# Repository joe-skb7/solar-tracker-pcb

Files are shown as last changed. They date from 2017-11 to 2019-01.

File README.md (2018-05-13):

# Solar tracker PCB

This project contains solar tracker PCB I made for my dad's project.

3D Model, Front View:

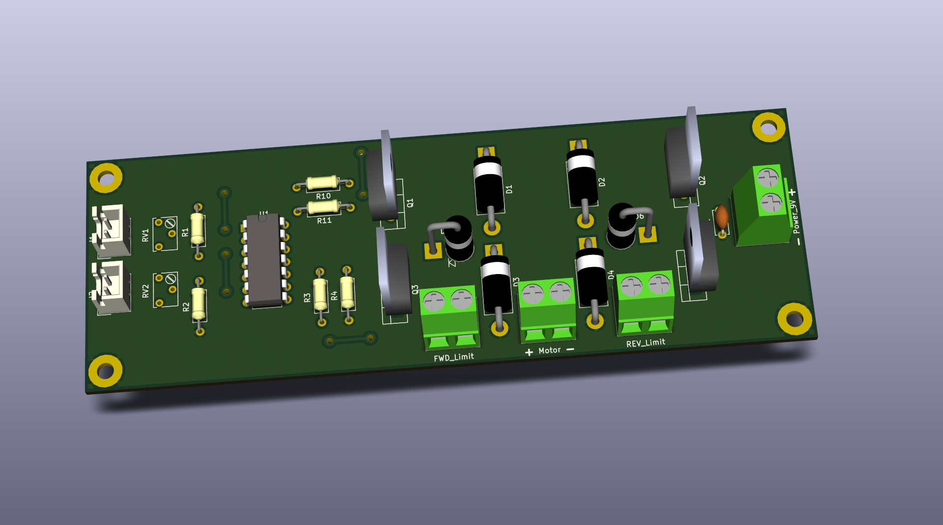
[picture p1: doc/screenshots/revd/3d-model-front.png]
3D Model, Front View


3D Model, Bottom View:

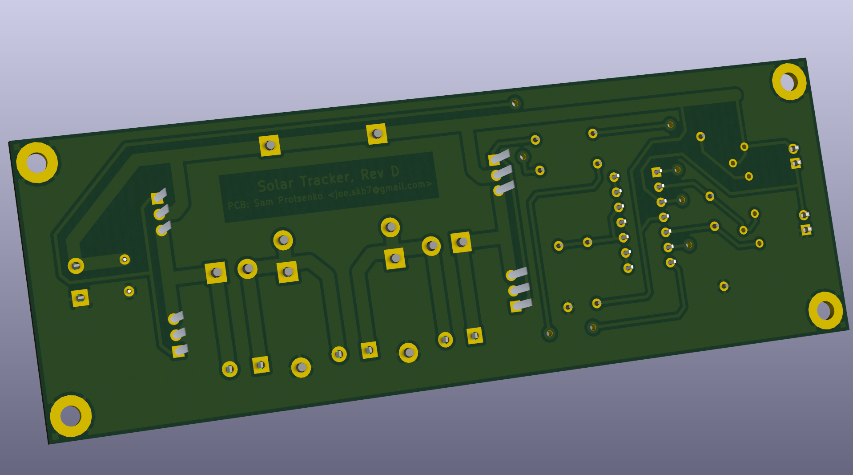
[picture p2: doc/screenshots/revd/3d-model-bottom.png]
3D Mode, Bottom View


Schematic:

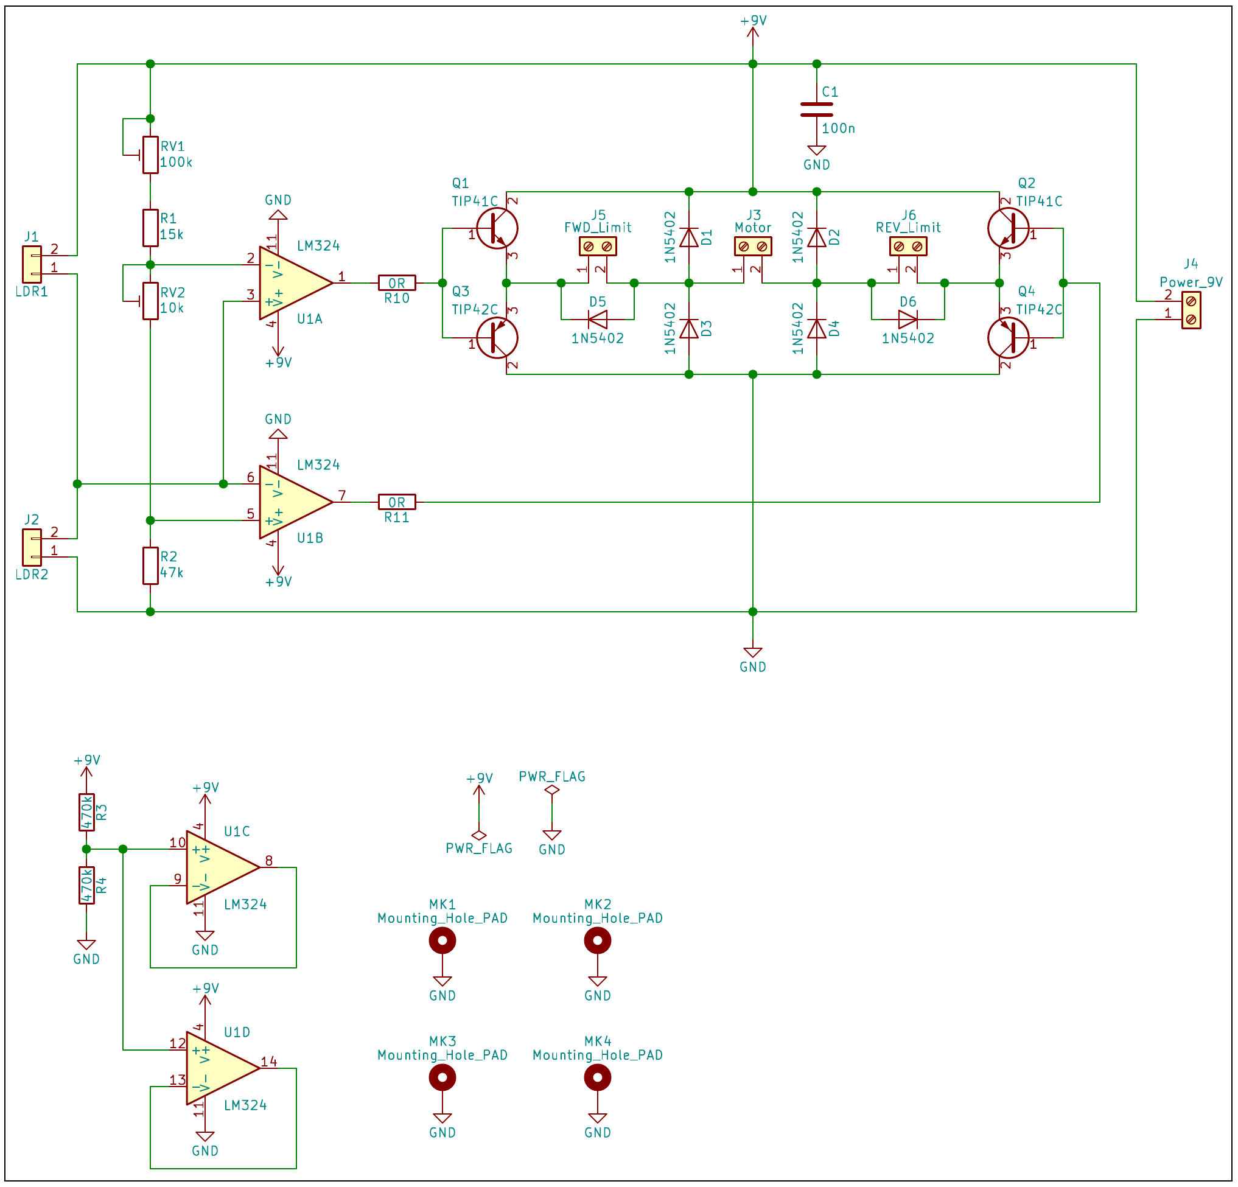
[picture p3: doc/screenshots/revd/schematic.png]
Schematic


I used KiCAD 4.0.7 for this PCB, but it should open fine in different versions,
as I keep `-cache.lib` file in this repo.

Original schematic can be found in `doc/scheme.jpg`. Things that I changed:
* properly terminated unused OPAMP parts
* added limit switches connection

## Schematic explanation

LDR1 and LDR2 photo-resistors yield signal which is used to determine in which
direction PV unit (solar panel) should be rotated, i.e. in which direction
we have more light radiation.

Signal from photo-resistors is being compared further by comparators built on
U1A and U1B OPAMPs. Reference voltage level is generated by dividers built on
R1, R2 resistors and RV1, RV2 trim-pots.

RV1 trim-pot is used to adjust this reference voltage point, so that motor
stands still when both photo-resistors are receiving the same light level.
RV2 is used to setup hysteresis level, so that motor is not moving when the
light difference on photo-resistors is small.

H-bridge formed by Q1-Q4 transistors is powering the motor, according to control
signals from comparators. Transistors are working in switch mode, as comparators
yield only 0 or VCC:

    V_out = 0,   if V+ < V-
    V_out = Vcc, if V+ > V-

D1-D4 are just flyback diodes, providing the path for back EMF discharge from
motor's coil, preventing other elements from it (transistors can be burnt, or
limit switches can be carbonized due to arcing).

C1 provides some of the energy required by the motor during the initial spike of
each turn-on.

R3 and R4 are used to properly terminate unused OPAMPs (U1C, U1D).

J5 and J6 terminal blocks (along with D5, D6 diodes) are used for connecting the
limit switches.

### Power consideration

Power voltage: 9V must be used. It's because the motor will receive only
`Vcc - 2.6` Volts, due to voltage drop across transistors and also on OPAMP,
as it's not Rail-to-Rail one. MG995 requires the voltage to be 4.8V ... 7.2V,
so the voltage drop must be accounted for.

Power current: 2A or more. Because MG995 can consume up to 1.5A on start
("stall current").

In case when 12V battery is used (it's common in solar panels appliance),
I suggest one to use external 12V-to-9V buck converter (2A rated, or more). It's
efficient (95%), small enough, and usually costs only $2-$3. No need to
over-complicate tracker schematic by adding voltage regulator scheme to it.

### Limit switches

`doc/limit-switch/` directory contains two possible schemes to implement limit
switches in H-bridge, with pros/cons overview. I personally like the second
scheme the best, so I implemented it in this project.

### EMI note

Notice that switching of DC motor's brushes leads to EMI, which may affect your
external circuits (especially digital ones, like MCUs). In that case you should
install EMI suppressor on your motor leads.

## Prepared files

`out/` directory contains ready to use files for manufacturing the PCB.

### Toner Transfer Method

See `out/toner-transfer-method/` for ready to use files.

Notes:
1. Remove the copper pour from both sides of PCB
2. Notice the Vias and front layer tracks. You need to solder jumper wires
   instead of them, in case if you are using single sided copper clad board.

### Manufacturing at plant

You can order the PCB to be manufactured on plant, e.g. at Seeed Studio (Fusion
PCB) or JLCPCB. Gerber files and drill file are prepared at `out/gerber/`.

## References

### Original scheme description and discussion

[1] http://www.electroschematics.com/8019/diy-solar-tracker-system/

[2] http://izobreteniya.net/solnechnyiy-treker-svoimi-rukami/

[3] http://radiokot.ru/forum/viewtopic.php?f=3&t=144321

[4] https://www.youtube.com/watch?v=UQyiuxo1Wvo

### Unused OPAMPs: proper termination

[5] https://www.electronicproducts.com/Analog_Mixed_Signal_ICs/Amplifiers/Properly_terminating_an_unused_op_amp.aspx

### EMI suppressor

[6] http://reprap.org/wiki/GM3_Noise_Suppressor_v1.0

## Authors

**Sam Protsenko**

## License

This project is licensed under the GPLv3.

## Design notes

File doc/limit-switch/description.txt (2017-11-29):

limit-switch-1.png
------------------

Pros:
 1. Easier to implement
 2. Limit switches can be low power rated

Cons:
 1. Transistor bases are floating in the air, when limit switch is activated;
    at least bases need to be pulled down
 2. Not a robust scheme: if transistor is broken, limit switch won't work

limit-switch-2.png
------------------

NOTE: flyback diodes are placed right next to motor, as they are for protecting
      the rest of the scheme from motor's back EMF. This way we can choose
      limit switches diodes for smaller voltage.

Pros:
 1. Robust scheme; limit switches are in motor circuit, so they will always
    work (even if transistors are broken)
 2. No need to pull-down transistors' bases

Cons:
 1. Limit switches must be high-power rated (big current)
 2. Additional two diodes are needed

We choose "limit-switch-2.png" option, as it's more robust and commonly adopted.

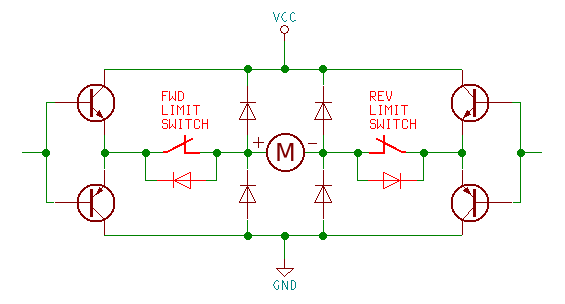
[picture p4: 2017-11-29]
doc/limit-switch/limit-switch-2.png

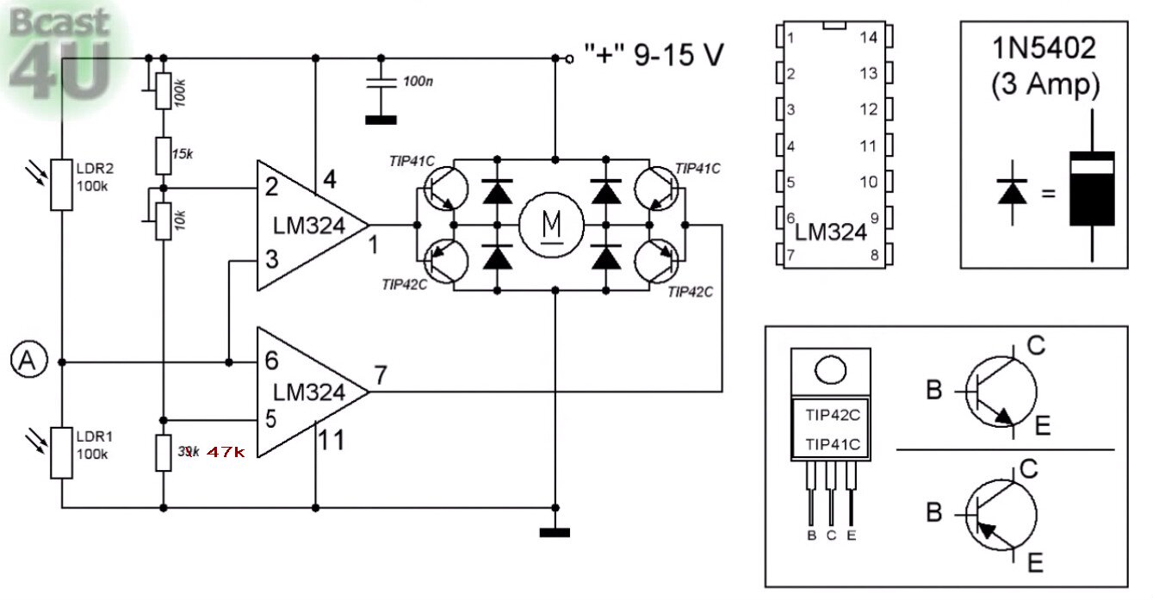
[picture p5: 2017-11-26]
doc/scheme.jpg

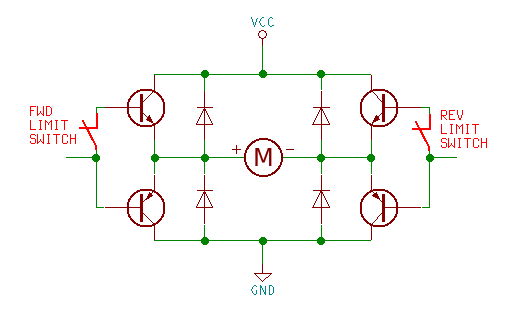
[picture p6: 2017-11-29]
doc/limit-switch/limit-switch-1.png

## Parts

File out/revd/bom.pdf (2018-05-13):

solar-tracker

Id | Designator | Package | Quantity | Designation
1 C1 | | C_Disc_D5.0mm_W2.5mm_P5.00mm | 1 100n
2 D1-D6 | | D_DO-201AD_P15.24mm_Horizontal | 6
3 J1,J2 | | JST_XH_B02B-XH-A_02x2.50mm_Straight | 2
4 J3-J6 | | TerminalBlock_Pheonix_MKDS1.5-2pol | 4
5 Q1,Q2 | | TO-220_Vertical | 2 TIP41C
6 Q3,Q4 | | TO-220_Vertical | 2 TIP42C
7 R1 | | R_Axial_DIN0207_L6.3mm_D2.5mm_P10.16mm_Horizontal | 1 15k
8 R10,R11 | | R_Axial_DIN0207_L6.3mm_D2.5mm_P10.16mm_Horizontal | 2 0R
9 R2 | | R_Axial_DIN0207_L6.3mm_D2.5mm_P10.16mm_Horizontal | 1 47k
10 R3,R4 | | R_Axial_DIN0207_L6.3mm_D2.5mm_P10.16mm_Horizontal | 2 470k
11 RV1 | | Potentiometer_Trimmer_Bourns_3266W | 1 100k
12 RV2 | | Potentiometer_Trimmer_Bourns_3266W | 1 10k
13 U1 | | DIP-14_W7.62mm | 1 LM324

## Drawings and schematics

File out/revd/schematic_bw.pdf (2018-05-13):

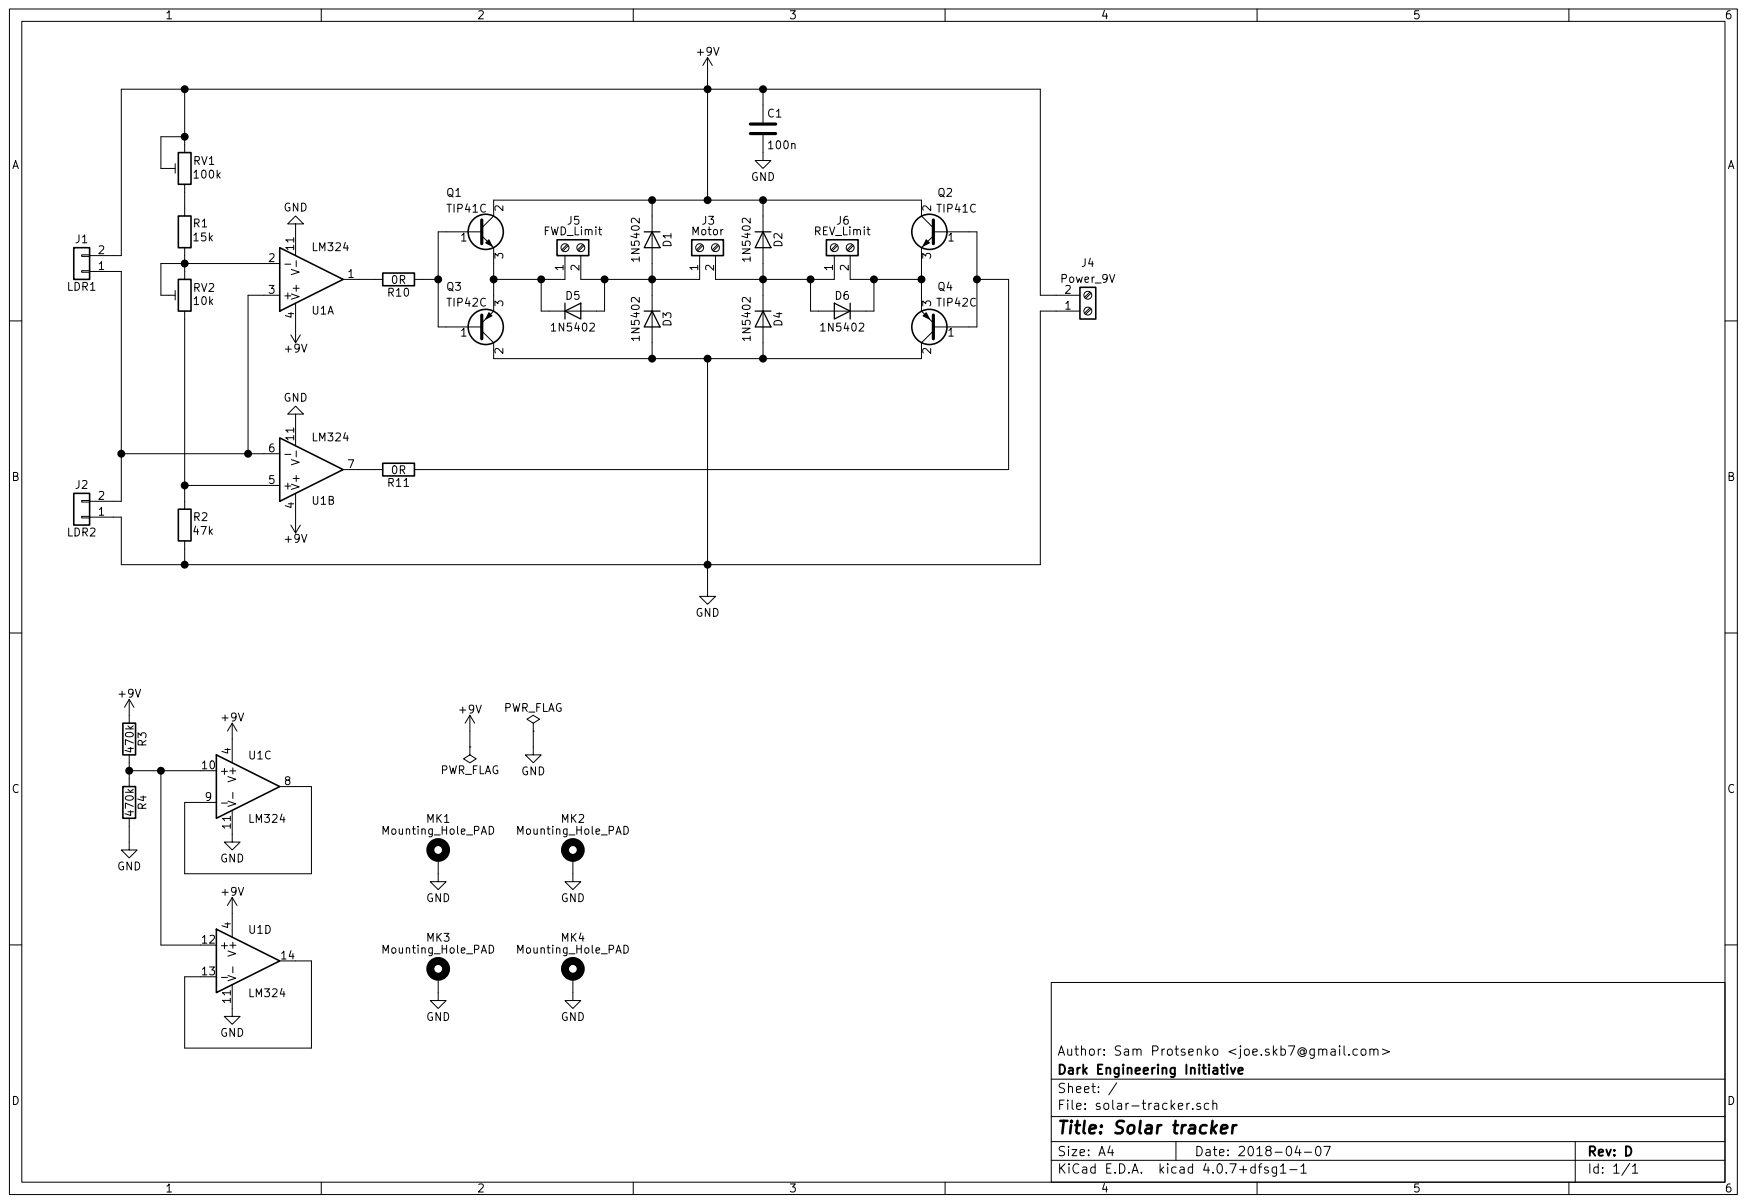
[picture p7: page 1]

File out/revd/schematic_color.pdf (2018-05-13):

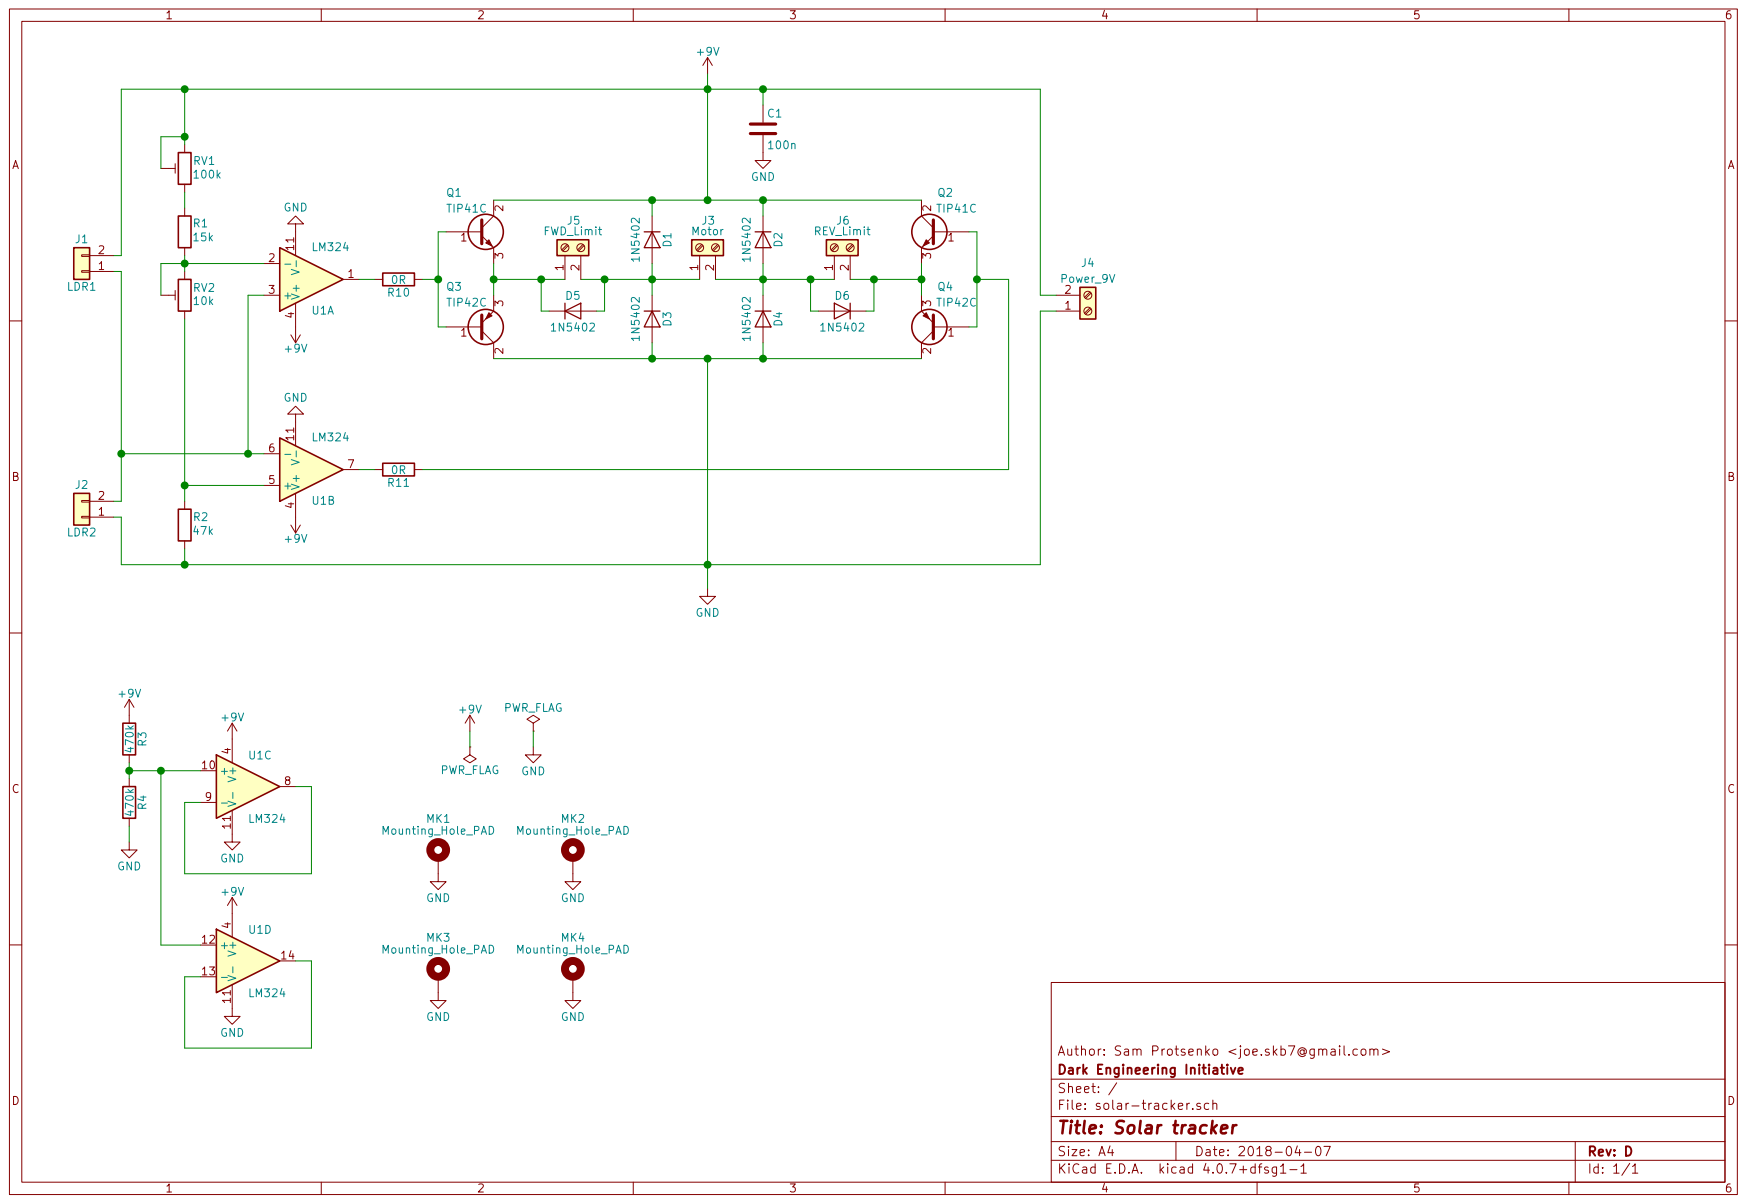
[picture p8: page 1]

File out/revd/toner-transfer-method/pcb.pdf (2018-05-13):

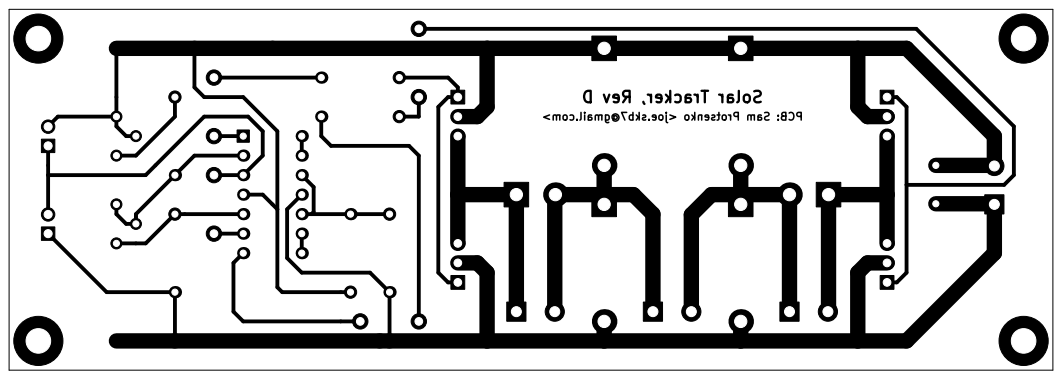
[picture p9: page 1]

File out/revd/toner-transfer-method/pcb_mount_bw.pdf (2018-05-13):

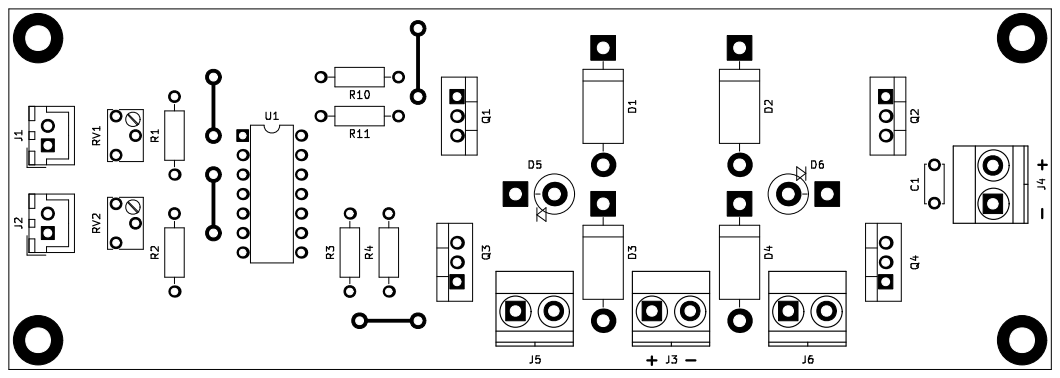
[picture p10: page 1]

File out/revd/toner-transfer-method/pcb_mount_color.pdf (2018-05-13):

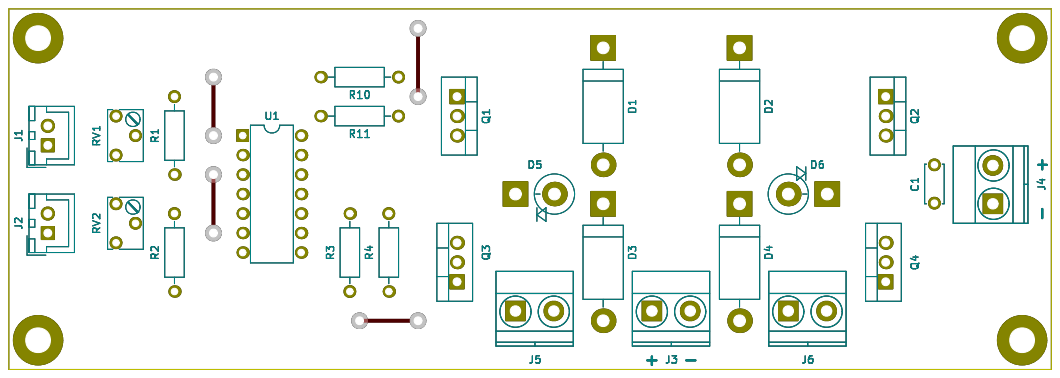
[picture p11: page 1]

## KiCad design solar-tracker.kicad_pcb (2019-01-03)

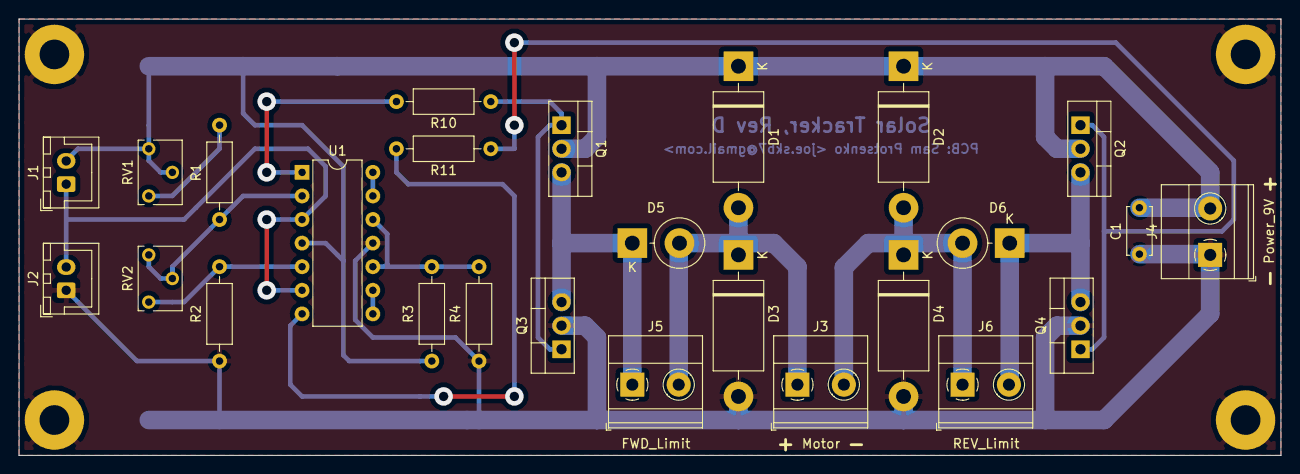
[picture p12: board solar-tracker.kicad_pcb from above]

Board: 2 copper layers, 135.9 x 47.0 mm, 30 parts (0 on the bottom side), 17 nets.

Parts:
C1: 100n; C_Disc_D5.0mm_W2.5mm_P5.00mm
D1, D2, D3, D4: 1N5402; D_DO-201AD_P15.24mm_Horizontal
D5, D6: 1N5402; D_DO-201AD_P5.08mm_Vertical_KathodeUp
J1: LDR1; JST_XH_B02B-XH-A_1x02_P2.50mm_Vertical
J2: LDR2; JST_XH_B02B-XH-A_1x02_P2.50mm_Vertical
J3: Motor; TerminalBlock_Phoenix_MKDS-1,5-2_1x02_P5.00mm_Horizontal
J4: Power_9V; TerminalBlock_Phoenix_MKDS-1,5-2_1x02_P5.00mm_Horizontal
J5: FWD_Limit; TerminalBlock_Phoenix_MKDS-1,5-2_1x02_P5.00mm_Horizontal
J6: REV_Limit; TerminalBlock_Phoenix_MKDS-1,5-2_1x02_P5.00mm_Horizontal
MK1, MK2, MK3, MK4: Mounting_Hole_PAD; MountingHole_3.2mm_M3_Pad
Q1, Q2: TIP41C; TO-220-3_Vertical
Q3, Q4: TIP42C; TO-220-3_Vertical
R1: 15k; R_Axial_DIN0207_L6.3mm_D2.5mm_P10.16mm_Horizontal
R2: 47k; R_Axial_DIN0207_L6.3mm_D2.5mm_P10.16mm_Horizontal
R3, R4: 470k; R_Axial_DIN0207_L6.3mm_D2.5mm_P10.16mm_Horizontal
R10, R11: 0R; R_Axial_DIN0207_L6.3mm_D2.5mm_P10.16mm_Horizontal
RV1: 100k; Potentiometer_Bourns_3266W_Vertical
RV2: 10k; Potentiometer_Bourns_3266W_Vertical
U1: LM324; DIP-14_W7.62mm

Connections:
+9V: C1.1, D1.1, D2.1, J1.2, J4.2, Q1.2, Q2.2, R3.1, RV1.1, RV1.2, U1.4
GND: C1.2, D3.2, D4.2, J2.1, J4.1, MK1.1, MK2.1, MK3.1, MK4.1, Q3.2, Q4.2, R2.2, R4.2, U1.11
unnamed: D1.2, D3.1, D5.2, J3.1, J5.2
unnamed: D2.2, D4.1, D6.2, J3.2, J6.1
unnamed: D5.1, J5.1, Q1.3, Q3.3
unnamed: D6.1, J6.2, Q2.3, Q4.3
unnamed: J1.1, J2.2, U1.3, U1.6
unnamed: Q1.1, Q3.1, R10.1
unnamed: Q2.1, Q4.1, R11.1
unnamed: R1.1, RV1.3
unnamed: R1.2, RV2.1, RV2.2, U1.2
unnamed: R2.1, RV2.3, U1.5
unnamed: R3.2, R4.1, U1.10, U1.12
unnamed: R10.2, U1.1
unnamed: R11.2, U1.7
unnamed: U1.8, U1.9
unnamed: U1.13, U1.14

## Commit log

2017-11-25 Add initial KiCAD files
    [solar-tracker.kicad_pcb, solar-tracker.sch]
2017-11-26 Started routing the PCB layout
    [solar-tracker.kicad_pcb, solar-tracker.sch]
2017-11-26 doc: Add original schematic
2017-11-26 Add cache lib
    -cache.lib: a local copy of all the symbols used in the corresponding
    schematic, so that when the folder containing a KiCad project is copied
    to a different PC, the schematic can still be opened and printed and
    will still look the same as the original draughtsperson intended - even
    if that other PC does not have those symbols in its main libraries
    (or has symbols that coincidentally have the same name but are
    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
2017-11-27 Create PCB layout for blocks
    [solar-tracker.kicad_pcb, solar-tracker.sch]
2017-11-27 Finish PCB
    [solar-tracker.kicad_pcb]
2017-11-27 pcb: Add PCB edges and copper pour
    [solar-tracker.kicad_pcb]
2017-11-27 pcb: Reduce via size
    [solar-tracker.kicad_pcb]
2017-11-27 schematic: Move unused OPAMP block to the right
    [solar-tracker.sch]
2017-11-27 pcb: Remove copper pour
    Prepare PCB for LUT (toner transfer method).
    [solar-tracker.kicad_pcb]
2017-11-27 schematic: Move C1 closer to H-bridge
    Where it belongs to.
    [solar-tracker.sch]
2017-11-27 pcb: Bring C1 close to H-bridge
    [solar-tracker.kicad_pcb]
2017-11-29 doc: Add limit switches schemes and description
2017-11-29 doc: Update limit switches schematic #2
    Move flyback diodes close to the motor, where they belong. While at it,
    add +/- labels on the motor and update the description.
2017-12-02 Update schematic and PCB to Revision B
    - Add limit switches + diodes
    - Vcc -> 9V
    - Use JST XH connectors for photo-resistors (instead of screw terminal
    blocks)
    - Add mounting holes to schematic
    - Bring back the copper pour; for Toner Transfer Method one can simply
    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
    [solar-tracker.kicad_pcb, solar-tracker.sch]
2017-12-02 out: Add ready to use files for manufacturing
    Also update README file, while at it.
    [solar-tracker-B.Cu.gbl, solar-tracker-Edge.Cuts.gm1, solar-tracker-F.Cu.gtl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]
2017-12-02 README: Add power consideration section
2017-12-02 README: Add limit switches note
2017-12-08 README: Add schematic screenshot
2018-04-07 Remove electrolytic capacitor
    It's slowing really slow, preventing to measure final voltage on unused
    OPAMPs terminals.
    [solar-tracker.kicad_pcb, solar-tracker.sch]
2018-04-07 Move old RevB files to corresponding directories
    [solar-tracker-B.Cu.gbl, solar-tracker-Edge.Cuts.gm1, solar-tracker-F.Cu.gtl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]
2018-05-13 schematic: Add means to separate control/power parts
    Add 0-Ohm R10, R11 so that user is able to separate control board from
    power board for debugging purposes.
    [solar-tracker.sch]
2018-05-13 pcb: Route PCB after adding R10, R11
    Route new circuit correspondingly.
    [solar-tracker.kicad_pcb]
2018-05-13 Update out/ and doc/
    Update all output files to Rev D.
    [solar-tracker-B.Cu.gbl, solar-tracker-Edge.Cuts.gm1, solar-tracker-F.Cu.gtl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]
2018-05-13 pcb: Add missing layers
    B.Mask and B.SilkS layers were missing by default. But they are needed
    for manufacturing (corresponding Gerber files must be generated). Enable
    those layers in:
    Design Rules -> Layers Setup
    and re-generate Gerber files.
    While at it, move terminal values to silk layer, which can be convenient
    for a user.
    [solar-tracker.kicad_pcb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]
2019-01-03 Migrate to KiCad 5.0
    [solar-tracker.kicad_pcb, solar-tracker.sch]
